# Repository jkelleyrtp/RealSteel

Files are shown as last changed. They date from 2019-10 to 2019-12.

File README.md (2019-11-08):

# FA19_POE_Final
Shadow-boxing robot using real-time pose estimation and a forward kinematic solver.

An exercise in high-speed Python, computer vision, point clouds, hardware iteration, and project management. 

Our public OnShape model is here:
    https://cad.onshape.com/documents/69187161d3d30544dff47cbf/w/b6740c08ed5948e4f2cbee36/e/f1060944df77cc7be88ce15a

## blog
The source files for the Hugo site generator.

## docs
The output of the hugo site generator

## scripts
Scripts to run various parts of the stack. All scripts are meant to be launched from the top level directory.

- `publishsite.sh` rebuilds the hugo site and pushes it to docs
- `launchapp.sh` runs python app in the correct environment

## robot
The DOF model for the robot to be displayed

## src
Primary application that runs the real steel experience.

## firmware
Firmware running on the microncontroller that responds to commands from app

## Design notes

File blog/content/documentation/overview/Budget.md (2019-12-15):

+++
title = "Budget"
weight = 40
+++

<center>

<table>
<tr>
<th>Item</th>
<th>Quantity</th>
<th>Price Per</th>
<th>Price Total</th>
</tr>
<tr>
<td>DC Motor 200 RPM</td>
<td>6</td>
<td>$15</td>
<td>$90</td>
</tr>
<tr>
<td>DC Motor Controller</td>
<td>6</td>
<td>$4</td>
<td>$24</td>
</tr>
<tr>
<td>5mm Shaft</td>
<td>2</td>
<td>$8</td>
<td>$16<br></td>
</tr>
<tr>
<td>3mm Shaft</td>
<td>1</td>
<td>$7</td>
<td>$7</td>
</tr>
<tr>
<td>M5 Bearing</td>
<td>4</td>
<td>$5</td>
<td>$20</td>
</tr>
<tr>
<td>M3 Bearing</td>
<td>10</td>
<td>$7</td>
<td>$70</td>
</tr>
<tr>
<td>Encoder</td>
<td>6</td>
<td>$2</td>
<td>$12</td>
</tr>
<tr>
<td>Hardware Kit</td>
<td>1</td>
<td>$15</td>
<td>$10</td>
</tr>
<tr>
<td>Total:</td>
<td></td>
<td></td>
<td>$249</td>
</tr>
<tr>
<td></td>
<td></td>
<td></td>
<td></td>
</tr>
<tr>
<td></td>
<td></td>
<td></td>
<td></td>
</tr>
</table>

</center>

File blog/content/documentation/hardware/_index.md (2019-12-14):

+++
title = "Hardware"
weight = 2
sort_by = "weight"
redirect_to = "documentation/content/overview"
insert_anchor_links = "left"
+++

Hardware
- High-level design
- Base
- Torso
- Arm
- Assembly

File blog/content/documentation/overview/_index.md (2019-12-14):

+++
title = "Overview"
weight = 1
sort_by = "weight"
redirect_to = "documentation/overview/overview"
insert_anchor_links = "left"
+++

Overview
 - Inspiration
 - Brainstorming
 - Constraints
 - Systems Design
 - Budget

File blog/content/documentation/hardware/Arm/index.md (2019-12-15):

+++
title = "Arm Design"
weight = 40
+++

The Real Steel robot arms were some of the most fun pieces to design of the whole system. We wanted to keep the mass of the arm as close to the axis of rotation as possible - the more balanced the arms were, the faster the motors could turn them. 

## Top-Level design

To simplify the design of the complicated sensor and motor interfaces, we created a single top-level sketch of the entire robot system and derived sketches for each of the subsystems. This approach to design is a common parametric technique that allows upstream design changes without breaking everything downstream. We were able to iterate on the width of the robot's shoulders and shoulder angles while the final pieces remained relatively the same. The benefits of this approach came to fruition when we modified the arm dimensions and mass in the final sprint by changing just a few numbers and reprinting all the pieces. 

We were particularly careful to keep the mass and size of the arm to a minimum. We gave special consideration to the placement of the servo and kept the center of mass as close to the shaft axis of rotation as possible. This gave the arm a fairly low mass moment of angular inertia. We used a simple linkage to transfer the servo's torque to the elbow which kept the weight down and allowed us to get a simple torque multiplier in with little effort. By maintaining a low profile on the arm components, the robot had a greater range of motion and could move fast enough for real-time movements. 

<center> {{ resize_image(path="documentation/hardware/Arm/Untitled.png", width=0, height=500, op="fit_height") }} </center>

<div class="row">
  <div class="column">
    <center> {{ resize_image(path="documentation/hardware/Arm/Untitled 3.png", width=0, height=300, op="fit_height") }} </center>
  </div>
  <div class="column">
    <center> {{ resize_image(path="documentation/hardware/Arm/Untitled 1.png", width=0, height=300, op="fit_height") }} </center>
  </div>
</div>

We were also careful to design with failure in mind. At the major interfaces, we chose to separate the single part into two parts fastened together. Specifically for the arm, the hub that connected it to the driving motor was removable from the primary arm component. We happened to print the dimensions improperly a few times before getting the design dialed in, and the separation between hub and arm was vital to keep the iteration time as fas as possible.

<center> {{ resize_image(path="documentation/hardware/Arm/Untitled 2.png", width=0, height=500, op="fit_height") }} </center>

<style>
    .row {
    display: flex;
    }

    .column {
    flex: 50%;
    }
</style>

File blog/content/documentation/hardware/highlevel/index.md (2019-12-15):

+++
title = "High Level Design"
weight = 10
+++

We faced a significant challenge in integrating the mechanical and electrical aspects of the project; each additional component added more complexity and points of failure. To mitigate the potential non-obvious potholes, we decided to start designing the system from a high-level first before diving into the details. 

Our mechanical system had a handful of requirements:

- The ability to "throw a punch"
- The ability to "bob and weave"
- The ability to "block a punch"

This ultimately manifested itself into a robot with:

- Two arms
- 3 DoF per arm (shoulder, proximal, and distal)
- 2 DoF hip system

Using OnShape as our CAD software of choice, we sketched out the high-level geometry, making sure to maintain realistic dimensions and leave room for important components like servos, motors, and sensors. The system sketch was used in "derive" mode to generate the rest of the subsystems.

<center> {{ resize_image(path="documentation/hardware/highlevel/Untitled.png", width=0, height=500, op="fit_height") }} </center>

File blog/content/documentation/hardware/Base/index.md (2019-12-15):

+++
title = "Base Design"
weight = 20
+++

The base of the robot underwent significant development. Early revisions were severely underspecced and not strong enough to hold the weight of the entire bot. 

The final design included 2 degrees of freedom - one for side-to-side movements and one for forward-to-backward movements - essentially pitch and roll. The dual fourbar design allowed the robot to move in both directions at once with design inspiration from joysticks. We used potentiometers to get feedback from the fourbars and a interesting method of embedded shaft to strength the prints.

<center> {{ resize_image(path="documentation/hardware/Base/Untitled.png", width=0, height=500, op="fit_height") }} </center>

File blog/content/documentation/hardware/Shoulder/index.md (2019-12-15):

+++
title = "Shoulder Design"
weight = 35
+++

The shoulders of the Real Steel robots were fun to design and pulled in some interesting 3D print techniques. We created an adapter system that used the profile of the motor shafts to fasten the hubs onto the primary body parts. This let us gracefully handle failures and more easily replace broken components. We also designed and 3D-printed our own gears which were used in conjunction with the custom encoder boards to get position feedback of the joints back to the STM32 controller. 

<div class="row">
  <div class="column">
    <center> {{ resize_image(path="documentation/hardware/Shoulder/Untitled.png", width=0, height=500, op="fit_height") }} </center>
  </div>
  <div class="column">
    <center> {{ resize_image(path="documentation/hardware/Shoulder/Untitled 2.png", width=0, height=500, op="fit_height") }} </center>
  </div>
</div>

<style>
    .row {
    display: flex;
    }

    .column {
    flex: 50%;
    }
</style>

One of the most interesting components of the shoulder system was the design of a custom parametric slew bearing which could adapt to any size we needed. We stuck with one size and honed in the sizes to be amenable for 3D printing. The slew bearings were able to take high axial and radial loads and were fast to manufacture. 

<center> {{ resize_image(path="documentation/hardware/Shoulder/Untitled 1.png", width=0, height=300, op="fit_height") }} </center>

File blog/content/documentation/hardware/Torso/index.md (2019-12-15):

+++
title = "Torso Design"
weight = 30
+++

The torso of the Real Steel robots was one of the more complicated parts of the robot to design. Not only did it have to integrate with the robot base, but it had to support both arms, the head, and the accompanying sensors to maintain accurate position control over the shoulder joints. The final design of the robot body came together in 5 separate pieces: the torso, the shoulder supports, the stand balance plate, and the head. 

The adapter plate was designed to simply bolt into the bottom of the primary torso part. We iterated several times on the adapter plate to allow for the "bob" and "weave" ranges of motion, and settled on the adapter plate design to allow for modifications to be made without having to reprint the torso. in fact, the torso itself is 3 separate pieces fastened together with bolts, plastic inserts, and CA glue.

<center>
    {{ resize_image(path="documentation/hardware/Torso/Untitled.png", width=0, height=500, op="fit_height") }}
</center>

We spent a lot of time iterating on the placement of motors and sensors on the torso. Shown below is the strange placement of the shoulder motor embedded deep into the torso. The wires were mostly inaccessible and had to be wired and soldered before installation. For proper assembly, the motor had to be dropped into the torso, the shoulder mound had to be fastened, and then we could finally mount the motor to the rest of the shoulder. However, the final design was very strong and with clever 3D printing, we achieved a robust torso design operating at near maximum PLA strength (more in some areas!) that gracefully took a few falls off the assembly table.

<center>
    {{ resize_image(path="documentation/hardware/Torso/Untitled 1.png", width=0, height=500, op="fit_height") }}
</center>

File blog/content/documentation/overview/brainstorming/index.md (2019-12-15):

+++
title = "Brainstorming + Inspiration"
weight = 20
+++

The idea to create a shadow boxing robot was nearly instant on the first team brainstorming night. Our  learning goals imposed an intense set of requirements on the project:

Machine Learning - Use AI/ML to provide a powerful HCI experience

Mechanical Iteration - Fabricate several iterations of a hardware-focused project

Kinematics - Do some complicated parallel math to build concurrency skills

Firmware - Use higher-end embedded architectures ARM/STM32

Closed-loop control - Implement a predictive control algorithm

Project Management - Get things done on time!

We ideated in one night, coming up with a handful of different projects we thought might properly satisfy the design constraints (notice the 5th idea):

<center>
    {{ resize_image(path="documentation/overview/Brainstorming/Untitled.png", width=0, height=500, op="fit_height") }}
</center>

## Night 1 Ideation

We initially imagined the shadow boxing robot as a pair of fighters - similar to the rock-em-sock robot game. Ultimately, we settled on a single fighter with a similar range of motion to that of the robots in the movie "Real Steel" - the 2011 action flick of the summer with Hugh Jackman and Dakota Goyo - one of our all-time personal favorite movies.

<center>
<div>

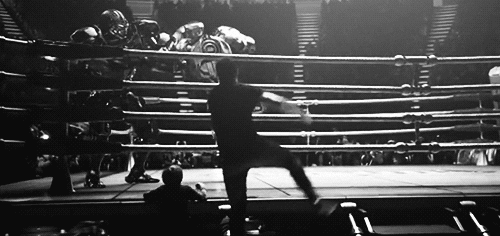
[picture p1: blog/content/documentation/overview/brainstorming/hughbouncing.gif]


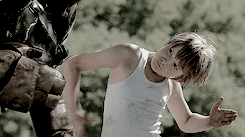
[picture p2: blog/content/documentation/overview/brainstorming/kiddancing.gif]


</div>
</center>

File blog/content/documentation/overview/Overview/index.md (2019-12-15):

+++
title = "Overview"
weight = 10
+++

This documentation provides a set of information and resources on how to design, build, and program and shadow-boxing robot for less than $250. This was an exceptionally ambitious Principles of Engineering project and required advanced skills in CAD, CAM, math, firmware, software, and systems integration. Each component of the system -  whether it be the serial output format of the robot joints or the location of the elbow linkage - was dependent on the other components. This led to an incredibly carefully designed collection of components that pushed the limits of Olin's 3D printers, the STM32 microcontroller, and the compute power of the school laptops. 

<center>
    {{ resize_image(path="documentation/overview/overview/reaganbot.png", width=0, height=500, op="fit_height") }}
</center>

## Final Feature Set

The final featureset of the Real Steel shadow-boxing robot is quite amazing:

- 8 Degrees of freedom - two arms and a hip system
- The ability to bob, weave, throw punches, and dab, all in real time
- 8 real-time PID controllers maintaining closed-loop control of the robot joint positions
- Real time pose estimation using a Time-of-Flight depth sensor
- Real-time kinematic solving of a 3 DoF robotic arm from a human's 7 DoF
- A portable Python-based multithreaded framework for data collection, processing, visualization, and serial output
- Pre-programmed positions for control without the kinect

## Challenges and Constraints

We ran into several challenges while designing and building the Real Steel robot. These included:

- Limited microcontroller inputs 12 quadrature encoders (2 robots worth, ran out after 1 robot)
- Limited outputs to control all the motor outputs
- Limited electrical power to power all motors simultaneously
- Limited compute power to process the kinect data and convert it into a serial packet with joint information
- Limited mechanical strength on 3D printed parts to handle the forces involved in moving the robot around

The following sections address these challenges and provide further insights on how the final feature set came together.

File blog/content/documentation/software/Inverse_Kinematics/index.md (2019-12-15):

+++
title = "Inverse Kinematics"
weight = 30
+++

## Inverse Kinematics

Inverse Kinematics is needed to map human movement into robot movement. This is because, calculating joint angles using human extracted joints doesn't translate to robot joint angles. We have different joints than the robot and at different positions and lengths. Instead, using an inverse kinematics solver an articulated body can be programmed to reach a certain target position with its end effector.

<center>


</center>

In RealSteel's robots, we have the following revolute joints in an arm:

1. Shoulder
2. Proximal
3. Distal

<center>
    {{ resize_image(path="documentation/software/Inverse_Kinematics/Untitled.png", width=0, height=500, op="fit_height") }}
</center>

### How Does It Work?

Given a target position, how can we position the articulated body and all it's joints such that the end effector reaches the target? An inverse kinematics solver answers this question with two categories of solutions:

1. Analytic solutions
2. Approximating solutions

We use ikpy, an inverse kinematics library, that can quickly approximate the solution with an iterative optimizer with regularization for smoothing.

<center>
    {{ resize_image(path="documentation/software/Inverse_Kinematics/Untitled 1.png", width=0, height=500, op="fit_height") }}
</center>

ikpy also can import the kinematic chain to solve as long as the robot is defined in URDF format. Luckily for us, we designed our own robot in OnShape and using onshape-to-robot we can convert our OnShape assembly to URDF robot definition.

### ikpy Coordinate System

ikpy defines its kinematic chain to start at the origin in a coordinate system that is rotated 90° about the x-axis compared to the Kinect coordinate system. We also run into an issue as the Kinect tracks joint positions with respect to a fixed origin at the center of it's camera lens and not at the base of the kinematic chain - the origin that ikpy expects. Therefore, any target position that we want to solve for with ikpy will be misinterpreted.

The solution is to transform the target joint's (the hand joint) position from the Kinect frame to a frame that has it's origin fixed at the shoulder joint of the arm that is being solved for. The z or depth value is then inverted to place depth in front of the person, and the point is rotated 90° about the x-axis. This way now the kinematic chain and target joint position are in the same frame of reference, and ikpy can solve correctly.

<center>
    {{ resize_image(path="documentation/software/Inverse_Kinematics/Untitled 2.png", width=0, height=400, op="fit_height") }}
</center>

### The Process

With all the tools in place, we can now proceed with solving for our robot joint angles in real-time in the following steps (note: this is done independently for both arms each)

1. Obtain robot model in URDF format
2. Import model into ikpy and define a base_element to start the kinematic chain at the shoulder joint of an arm
3. Obtain target position from the Kinect → the world coordinates for skeletal joint at the hand for the corresponding arm
4. Perform the necessary transforms to get the target into ikpy coordinate system
5. Solve for joint angles

[https://youtu.be/kSUGiyJ5UbY](https://youtu.be/kSUGiyJ5UbY)

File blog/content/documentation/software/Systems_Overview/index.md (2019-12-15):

+++
title = "Software Overview"
weight = 10
+++

The software powering Real Steel is fairly complex, but we chose a handful of architectural patterns and libraries to simplify the development process. Our language of choice was Python and we relied heavily on `OpenNI` for kinect-related libraries, Python's `Multiprocessing` library for concurrency, `ikpy` for forward kinematic solving, `pybullet` for simulation of the robot, and `PySerial` to get the joint angle to the robot.

<center>
    {{ resize_image(path="documentation/software/Systems_Overview/Untitled.png", width=0, height=500, op="fit_height") }}
</center>

All of these components were given their own `class` in the Python code, and inherited certain functionality so that we could easily disable and enable different parts of the code with a few flags. For instance, the python code that loads in all the modules is fairly simple, despite the entire codebase being several thousand lines. We chose the pipeline architecture and separated each of the components into their own submodules to be more easily unit-testable. The entire system can run with "fake" components which satisfy the software requirements and even create fake data so we can do integration tests with entire chunks of the pipeline missing. This is a solid, industry-practiced software engineering tactic that allowed us to iterate faster and modularize our code.

```python
from realsteel.device import ROBOT_DEVICE, FAKE_DEVICE
from realsteel.visualizer import DEMO_VIS, ROBOT_VIS, FAKE_VIS
from realsteel.joint_input import CAMERA, KINECT, HYBRID
from realsteel.kinematic import KSOLVER
from realsteel.pathplanner import PATHPLANNER
from realsteel.kinematic import ArmJoints

class ROBOT:
    """
    This code processes the launch args and sets up all the moving parts to get the REAL STEEL experience up and running.
    Nothing in this main loop should blocking, but rather pushing data around between threads. Everything should be async.

    """
    def __init__(self, hardware_enabled = False, visualization_mode="disabled"):
        # [1] Build the virtual robot from joints
        # [2] Set up the camera/kinect inputs to dump raw joint angles
        # [3] Set up the kinematic solver that takes raw joint angles and turns into robot angles
        # [4] Set up the path planner that maps joint angles frames
        # [5] Set up the physical robot interface
        # [6] Set up the visualizer

        # Process the user flags to process things like dev mode
        self.hardware_enabled: bool = hardware_enabled
        self.visualization_mode = visualization_mode

        # [1] Build the robot from a URDF file
        # TODO, allow specifying a custon URDF
        self.human_positions: dict = None
        self.robot_positions: dict = None
        # self.intialize_robot_from_urdf(file = "")

        # [2] Set up the camera/kinect input device
        self.joint_input = HYBRID()

        # [3] Set up the kinematic solver 
        self.solver = KSOLVER()

        # [4] Set up the path planner
        self.planner = PATHPLANNER()

        # [5] Set up the hardware device
        if self.hardware_enabled:
            self.device = ROBOT_DEVICE()
        else:
            self.device = FAKE_DEVICE()

        # [6] Set up the visualizer
        if self.visualization_mode == "dev":
            self.visualizer = ROBOT_VIS(directory='robot/')

        elif self.visualization_mode == "demo":
            self.visualizer = DEMO_VIS()

        else:
            self.visualizer = FAKE_VIS()
```

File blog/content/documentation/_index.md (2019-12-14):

+++
template = "documentation.html"
redirect_to = "documentation/overview/"
+++

Overview
Overview
Inspiration
Brainstorming
Constraints
Systems Design
Budget
 
Hardware
High-level design
Base
Torso
Arm
Assembly

Electrical and Firmware
Sensors
Schematic
Firmware overview
Control loops and feedback

Software
Human Tracking
PyBullet
Kinematics Tracking
Multithreading
Serial Output

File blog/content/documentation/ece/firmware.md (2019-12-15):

+++
title = "Firmware Overview"
weight = 10
+++

The robot firmware had one job: take a setpoint over serial and maintain closed-loop control over the robot subsystems. We used PWM to communicate with each of the motor controllers and an external power supply to power everything, so the firmware simply needed to output a signal for each motor. 

The setpoint came in over serial and was decoded by a custom bson interpreter written in C++. We used the STM32 chip on the Nucleo F446ZE development board as the microcontroller, and reused PID control from the last PoE lab for closed-loop control. As our port and compute capacity was limited, the predictive control was all implemented on the host software.

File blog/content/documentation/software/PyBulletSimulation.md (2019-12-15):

+++
title = "PyBullet Simulation"
weight = 40
+++

## PyBullet Simulation

Before we send the joint coordinates over serial to the actual robot, we want to ensure that our methodology and solutions are correct. Therefore, we use PyBullet, a physics engine, to simulate our robot movements.

<center>
    {{ resize_image(path="documentation/software/Inverse_Kinematics/Untitled 3.png", width=0, height=200, op="fit_height") }}
</center>

Loading in our URDF file for the robot, we can pump in the joint angles and see how a virtual replica of our robot would behave under proper physics.

[https://youtu.be/1XufNJylf4Q](https://youtu.be/1XufNJylf4Q)

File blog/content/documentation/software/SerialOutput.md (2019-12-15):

+++
title = "Serial Output"
weight = 60
+++

To communicate with the Real Steel robots, we initialized a serial interface with the STM32 microcontroller (the robot's brain) to send joint positions and other information. We set up the serial interface in a separate thread as to not slow down the main thread responsible for moving data in between each of the system components. This let us maintain a 1 kHz control loop between the master computer and Real Steel robot without any performance impact on the rest of the software system.

To communicate, we used the bson minified data format - a compressed version of csv with a fixed schema based on packet length. We also developed a custom interpreter for the STM32 as there were no obvious choices that fit on an embedded system to interpret the serial data. The final format for commands between the computer and robot followed as such:

```rust
#[derive(debug, fmt)]
enum MessageTypes {
	setpoint(RobotSetpoint)
}

impl serialize for MessageTypes {
	fn serialize() -> String {
		match Self {
			MessageTypes::setpoint(setpoint) -> {
				return format!(
					"0",
					setpoint.left_shoulder,
					setpoint.left_proximal,
					setpoint.left_distal: usize,
					setpoint.right_shoulder,
					setpoint.right_proximal,
					setpoint.right_distal,
					pitch: usize,
					roll: uszie
				)
			}
		}
	}
}

#[derive(debug, fmt)]
struct RobotSetpoint {
	left_shoulder: usize,
	left_proximal: usize,
	left_distal: usize,
	right_shoulder: usize,
	right_proximal: usize,
	right_distal: usize,
	pitch: usize,
	roll: uszie
}
```

With this format, we could easily serialize and deserialize robot setpoints from the kinematic solver and convert them into a message that the robot could interpret. Messages could be of variable length, with the expected length determined by the leading digit for the packet. As shown above, the leading digit for the RobotSetpoint is 0 - so the stm32 can easily decode the robot position over a simple serial packet.

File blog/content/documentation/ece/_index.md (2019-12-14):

+++
title = "Electrical and Firmware"
weight = 3
sort_by = "weight"
redirect_to = "documentation/ece/Firmwareoverview"
insert_anchor_links = "left"
+++

Overview
 - Inspiration
 - Brainstorming
 - Constraints
 - Systems Design
 - Budget

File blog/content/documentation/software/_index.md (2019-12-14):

+++
title = "Software"
weight = 1
sort_by = "weight"
redirect_to = "documentation/software/overview.md"
insert_anchor_links = "left"
+++

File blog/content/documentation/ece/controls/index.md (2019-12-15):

+++
title = "Controls and Feedback"
weight = 30
+++

## Motor control:

A simple PID controller was used for motor control. However, we were able to run it at 1kHz due to the floating point accelerator on the STM32F446, allowing for extremely high gain feedback.

## Motor controller boards:

We decided to be thrifty and copied 1:1 Adafruit's DRV8871 motor controller boards, saving us a large amount of money compared to what we'd have to spend on 12 genuine ones.

<center> {{ resize_image(path="documentation/ece/controls/Untitled.png", width=0, height=500, op="fit_height") }} </center>

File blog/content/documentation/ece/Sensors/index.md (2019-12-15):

+++
title = "Sensors"
weight = 20
+++

We designed a handful of custom sensor to make the feedback collection easier. One important sensor we designed was a simple quadrature encoder board with a dial knob. This allowed us to integrate the gears onto the encoders with ease, and each board was exceptionally cheap at only $2 per.

<center> {{ resize_image(path="documentation/ece/Sensors/Untitled.png", width=0, height=500, op="fit_height") }} </center>

As 8 quadrature encoders is simply too much information for the STM32 to handle at once, we also developed a simple quadrature interpreter board after we had designed the quadrature encoders. This counted the number of steps the quadrature encoder had performed and stored them so the firmware wouldn't have to keep track manually. These boards were powered by a simple STM8 and output their data over I2C. This gave us an incredible performance boost and allowed us to keep closed-loop control of the robot arms and hip system without the controller breaking a sweat.

<center> {{ resize_image(path="documentation/ece/Sensors/Untitled 1.png", width=0, height=500, op="fit_height") }} </center>

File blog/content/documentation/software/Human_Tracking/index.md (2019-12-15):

+++
title = "Human Tracking"
weight = 20
+++

## Human Tracking

We use the Kinect v1 camera to perform human skeleton tracking using its IR camera. We interface with the Kinect using the OpenNI2 library for core Kinect features and NiTE2 for skeleton tracking purposes. To support the Kinect v1 camera with these two libraries, the OpenNI2-FreenectDriver bridge must also be installed. These libraries allow us to develop in non-windows platforms using opensource software.

### Dependency Installation

There are difficulties in getting these dependencies installed as the OpenNI and NiTE project was discontinued when Apple bought PrimeSense. Instead, these packages are now hosted and can be downloaded using the following guide:

[https://github.com/roboticslab-uc3m/installation-guides/blob/master/install-openni-nite.md](https://github.com/roboticslab-uc3m/installation-guides/blob/master/install-openni-nite.md)

### Skeleton Tracking

Using NiTE2 we access skeleton tracking information from the Kinect. At each frame we obtain the position of all 15 joints as (x, y, z) coordinates. 

<center>

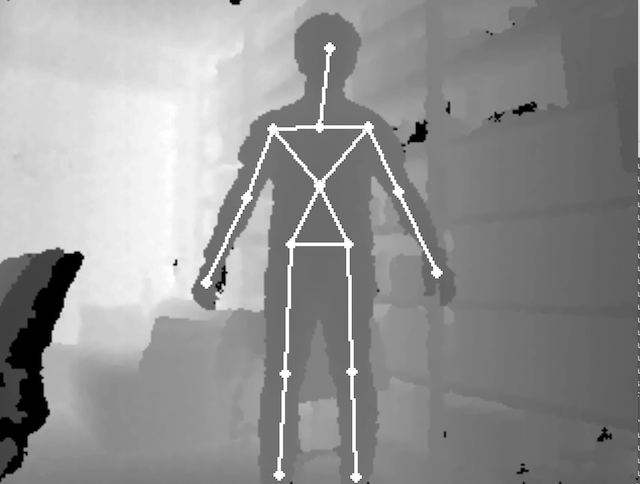
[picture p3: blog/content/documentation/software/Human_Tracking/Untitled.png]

</center>

### Coordinate System

The Kinect and OpenNI has two coordinate systems used. These two systems are referred to as Depth and World representation. The differences can be described like so:

1. Depth coordinates
    - the native data representation
    - the origin is the top-left corner of the field of view
    - x and y coordinates are reference to the image frame pixels
    - the depth value represents the distance between the camera plane and whatever object is in the given pixel
2. World coordinates
    - superimpose a more familiar 3D Cartesian coordinate system on the world
    - the origin is at the Kinect camera lens
    - every point is specified by 3 points (x, y , z) in millimeters

<center>

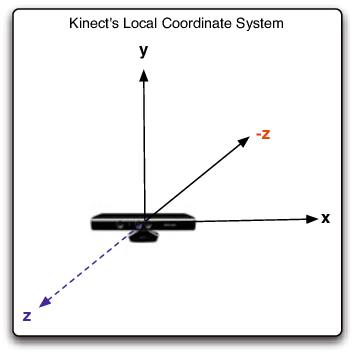
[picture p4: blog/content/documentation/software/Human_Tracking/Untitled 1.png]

</center>

We obtain the joint information and can convert between both systems depending on our needs.

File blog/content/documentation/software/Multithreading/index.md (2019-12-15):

+++
title = "Multithreaded Framework"
weight = 50
+++

## Multithreaded Framework

In order to perform the skeleton tracking, joint solving, visualizations, and communication all together  simultaneously, we set up a multithreaded framework centered around python's multiprocessing Queues. In our framework, we use two queues: an input queue and a device/output queue. 

The input queue gets Kinect joint information pushed into it at every frame. The other systems, inverse kinematics and visualizations, pop joint information off of this queue as long as it's not empty for processing.

The device queue gets robot joint angles pushed into it at every iteration of the main robot loop and communicates these angles over serial whenever they are available.

```python
def main_loop(self):
	# Set up a shared queue to put human angles into
	input_queue = Queue()

	# Get the process for the input method and start it
	input_proc = self.joint_input.launch(input_queue)
	input_proc.start()
	
	# Set up the device queue to push data into
	device_queue = Queue()
	device_proq = self.device.launch(device_queue)
	device_proq.start()
	
	# Set the initial joint angles
	joints = {}
	joint_angles = [1, 1]
	
	while True:
		# Check if there's a new human joint inputs ready
		# if not input_queue.empty():
		joints = input_queue.get()
		if joints['Lwri']:
			joint_angles = self.solver.solve(joints['Lwri']['pc'])
	
			joint = ArmJoints(joint_angles[0], joint_angles[1], 0.0)
	
			device_queue.push(joint)
```

This architecture is the exact same architecture used in microprocessors and the technique is known as "pipelining." Just by properly designing the architecture of our code, we saw up to 60-80% performance improvement which was crucial for real time actuation.

<center>
    {{ resize_image(path="documentation/software/Multithreading/Untitled.png", width=0, height=500, op="fit_height") }}
</center>

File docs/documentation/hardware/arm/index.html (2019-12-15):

- Overview
  - Overview (https://jonathan-kelley.com/FA19_POE_Final/documentation/overview/overview/)
  - Brainstorming + Inspiration (https://jonathan-kelley.com/FA19_POE_Final/documentation/overview/brainstorming/)
  - Budget (https://jonathan-kelley.com/FA19_POE_Final/documentation/overview/budget/)
- Software
  - Software Overview (https://jonathan-kelley.com/FA19_POE_Final/documentation/software/systems-overview/)
  - Human Tracking (https://jonathan-kelley.com/FA19_POE_Final/documentation/software/human-tracking/)
  - Inverse Kinematics (https://jonathan-kelley.com/FA19_POE_Final/documentation/software/inverse-kinematics/)
  - PyBullet Simulation (https://jonathan-kelley.com/FA19_POE_Final/documentation/software/pybulletsimulation/)
  - Multithreaded Framework (https://jonathan-kelley.com/FA19_POE_Final/documentation/software/multithreading/)
  - Serial Output (https://jonathan-kelley.com/FA19_POE_Final/documentation/software/serialoutput/)
- Hardware
  - High Level Design (https://jonathan-kelley.com/FA19_POE_Final/documentation/hardware/highlevel/)
  - Base Design (https://jonathan-kelley.com/FA19_POE_Final/documentation/hardware/base/)
  - Torso Design (https://jonathan-kelley.com/FA19_POE_Final/documentation/hardware/torso/)
  - Shoulder Design (https://jonathan-kelley.com/FA19_POE_Final/documentation/hardware/shoulder/)
  - Arm Design (https://jonathan-kelley.com/FA19_POE_Final/documentation/hardware/arm/)
  - Assembly (https://jonathan-kelley.com/FA19_POE_Final/documentation/hardware/assembly/)
- Electrical and Firmware
  - Firmware Overview (https://jonathan-kelley.com/FA19_POE_Final/documentation/ece/firmware/)
  - Sensors (https://jonathan-kelley.com/FA19_POE_Final/documentation/ece/sensors/)
  - Controls and Feedback (https://jonathan-kelley.com/FA19_POE_Final/documentation/ece/controls/)

# Arm Design

The Real Steel robot arms were some of the most fun pieces to design of the whole system. We wanted to keep the mass of the arm as close to the axis of rotation as possible - the more balanced the arms were, the faster the motors could turn them.

## 🔗Top-Level design

To simplify the design of the complicated sensor and motor interfaces, we created a single top-level sketch of the entire robot system and derived sketches for each of the subsystems. This approach to design is a common parametric technique that allows upstream design changes without breaking everything downstream. We were able to iterate on the width of the robot's shoulders and shoulder angles while the final pieces remained relatively the same. The benefits of this approach came to fruition when we modified the arm dimensions and mass in the final sprint by changing just a few numbers and reprinting all the pieces.

We were particularly careful to keep the mass and size of the arm to a minimum. We gave special consideration to the placement of the servo and kept the center of mass as close to the shaft axis of rotation as possible. This gave the arm a fairly low mass moment of angular inertia. We used a simple linkage to transfer the servo's torque to the elbow which kept the weight down and allowed us to get a simple torque multiplier in with little effort. By maintaining a low profile on the arm components, the robot had a greater range of motion and could move fast enough for real-time movements.







We were also careful to design with failure in mind. At the major interfaces, we chose to separate the single part into two parts fastened together. Specifically for the arm, the hub that connected it to the driving motor was removable from the primary arm component. We happened to print the dimensions improperly a few times before getting the design dialed in, and the separation between hub and arm was vital to keep the iteration time as fas as possible.



©2017-2019 — Jonathan Kelley (https://jonathan-kelley.com) and contributors (https://github.com/jkelleyrtp/FA19_POE_Final/graphs/contributors)

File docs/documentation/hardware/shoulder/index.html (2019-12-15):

- Overview
  - Overview (https://jonathan-kelley.com/FA19_POE_Final/documentation/overview/overview/)
  - Brainstorming + Inspiration (https://jonathan-kelley.com/FA19_POE_Final/documentation/overview/brainstorming/)
  - Budget (https://jonathan-kelley.com/FA19_POE_Final/documentation/overview/budget/)
- Software
  - Software Overview (https://jonathan-kelley.com/FA19_POE_Final/documentation/software/systems-overview/)
  - Human Tracking (https://jonathan-kelley.com/FA19_POE_Final/documentation/software/human-tracking/)
  - Inverse Kinematics (https://jonathan-kelley.com/FA19_POE_Final/documentation/software/inverse-kinematics/)
  - PyBullet Simulation (https://jonathan-kelley.com/FA19_POE_Final/documentation/software/pybulletsimulation/)
  - Multithreaded Framework (https://jonathan-kelley.com/FA19_POE_Final/documentation/software/multithreading/)
  - Serial Output (https://jonathan-kelley.com/FA19_POE_Final/documentation/software/serialoutput/)
- Hardware
  - High Level Design (https://jonathan-kelley.com/FA19_POE_Final/documentation/hardware/highlevel/)
  - Base Design (https://jonathan-kelley.com/FA19_POE_Final/documentation/hardware/base/)
  - Torso Design (https://jonathan-kelley.com/FA19_POE_Final/documentation/hardware/torso/)
  - Shoulder Design (https://jonathan-kelley.com/FA19_POE_Final/documentation/hardware/shoulder/)
  - Arm Design (https://jonathan-kelley.com/FA19_POE_Final/documentation/hardware/arm/)
  - Assembly (https://jonathan-kelley.com/FA19_POE_Final/documentation/hardware/assembly/)
- Electrical and Firmware
  - Firmware Overview (https://jonathan-kelley.com/FA19_POE_Final/documentation/ece/firmware/)
  - Sensors (https://jonathan-kelley.com/FA19_POE_Final/documentation/ece/sensors/)
  - Controls and Feedback (https://jonathan-kelley.com/FA19_POE_Final/documentation/ece/controls/)

# Shoulder Design

The shoulders of the Real Steel robots were fun to design and pulled in some interesting 3D print techniques. We created an adapter system that used the profile of the motor shafts to fasten the hubs onto the primary body parts. This let us gracefully handle failures and more easily replace broken components. We also designed and 3D-printed our own gears which were used in conjunction with the custom encoder boards to get position feedback of the joints back to the STM32 controller.





One of the most interesting components of the shoulder system was the design of a custom parametric slew bearing which could adapt to any size we needed. We stuck with one size and honed in the sizes to be amenable for 3D printing. The slew bearings were able to take high axial and radial loads and were fast to manufacture.



©2017-2019 — Jonathan Kelley (https://jonathan-kelley.com) and contributors (https://github.com/jkelleyrtp/FA19_POE_Final/graphs/contributors)

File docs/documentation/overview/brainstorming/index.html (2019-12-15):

- Overview
  - Overview (https://jonathan-kelley.com/FA19_POE_Final/documentation/overview/overview/)
  - Brainstorming + Inspiration (https://jonathan-kelley.com/FA19_POE_Final/documentation/overview/brainstorming/)
  - Budget (https://jonathan-kelley.com/FA19_POE_Final/documentation/overview/budget/)
- Software
  - Software Overview (https://jonathan-kelley.com/FA19_POE_Final/documentation/software/systems-overview/)
  - Human Tracking (https://jonathan-kelley.com/FA19_POE_Final/documentation/software/human-tracking/)
  - Inverse Kinematics (https://jonathan-kelley.com/FA19_POE_Final/documentation/software/inverse-kinematics/)
  - PyBullet Simulation (https://jonathan-kelley.com/FA19_POE_Final/documentation/software/pybulletsimulation/)
  - Multithreaded Framework (https://jonathan-kelley.com/FA19_POE_Final/documentation/software/multithreading/)
  - Serial Output (https://jonathan-kelley.com/FA19_POE_Final/documentation/software/serialoutput/)
- Hardware
  - High Level Design (https://jonathan-kelley.com/FA19_POE_Final/documentation/hardware/highlevel/)
  - Base Design (https://jonathan-kelley.com/FA19_POE_Final/documentation/hardware/base/)
  - Torso Design (https://jonathan-kelley.com/FA19_POE_Final/documentation/hardware/torso/)
  - Shoulder Design (https://jonathan-kelley.com/FA19_POE_Final/documentation/hardware/shoulder/)
  - Arm Design (https://jonathan-kelley.com/FA19_POE_Final/documentation/hardware/arm/)
  - Assembly (https://jonathan-kelley.com/FA19_POE_Final/documentation/hardware/assembly/)
- Electrical and Firmware
  - Firmware Overview (https://jonathan-kelley.com/FA19_POE_Final/documentation/ece/firmware/)
  - Sensors (https://jonathan-kelley.com/FA19_POE_Final/documentation/ece/sensors/)
  - Controls and Feedback (https://jonathan-kelley.com/FA19_POE_Final/documentation/ece/controls/)

# Brainstorming + Inspiration

The idea to create a shadow boxing robot was nearly instant on the first team brainstorming night. Our learning goals imposed an intense set of requirements on the project:

Machine Learning - Use AI/ML to provide a powerful HCI experience

Mechanical Iteration - Fabricate several iterations of a hardware-focused project

Kinematics - Do some complicated parallel math to build concurrency skills

Firmware - Use higher-end embedded architectures ARM/STM32

Closed-loop control - Implement a predictive control algorithm

Project Management - Get things done on time!

We ideated in one night, coming up with a handful of different projects we thought might properly satisfy the design constraints (notice the 5th idea):



## 🔗Night 1 Ideation

We initially imagined the shadow boxing robot as a pair of fighters - similar to the rock-em-sock robot game. Ultimately, we settled on a single fighter with a similar range of motion to that of the robots in the movie "Real Steel" - the 2011 action flick of the summer with Hugh Jackman and Dakota Goyo - one of our all-time personal favorite movies.





©2017-2019 — Jonathan Kelley (https://jonathan-kelley.com) and contributors (https://github.com/jkelleyrtp/FA19_POE_Final/graphs/contributors)

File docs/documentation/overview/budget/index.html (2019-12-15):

- Overview
  - Overview (https://jonathan-kelley.com/FA19_POE_Final/documentation/overview/overview/)
  - Brainstorming + Inspiration (https://jonathan-kelley.com/FA19_POE_Final/documentation/overview/brainstorming/)
  - Budget (https://jonathan-kelley.com/FA19_POE_Final/documentation/overview/budget/)
- Software
  - Software Overview (https://jonathan-kelley.com/FA19_POE_Final/documentation/software/systems-overview/)
  - Human Tracking (https://jonathan-kelley.com/FA19_POE_Final/documentation/software/human-tracking/)
  - Inverse Kinematics (https://jonathan-kelley.com/FA19_POE_Final/documentation/software/inverse-kinematics/)
  - PyBullet Simulation (https://jonathan-kelley.com/FA19_POE_Final/documentation/software/pybulletsimulation/)
  - Multithreaded Framework (https://jonathan-kelley.com/FA19_POE_Final/documentation/software/multithreading/)
  - Serial Output (https://jonathan-kelley.com/FA19_POE_Final/documentation/software/serialoutput/)
- Hardware
  - High Level Design (https://jonathan-kelley.com/FA19_POE_Final/documentation/hardware/highlevel/)
  - Base Design (https://jonathan-kelley.com/FA19_POE_Final/documentation/hardware/base/)
  - Torso Design (https://jonathan-kelley.com/FA19_POE_Final/documentation/hardware/torso/)
  - Shoulder Design (https://jonathan-kelley.com/FA19_POE_Final/documentation/hardware/shoulder/)
  - Arm Design (https://jonathan-kelley.com/FA19_POE_Final/documentation/hardware/arm/)
  - Assembly (https://jonathan-kelley.com/FA19_POE_Final/documentation/hardware/assembly/)
- Electrical and Firmware
  - Firmware Overview (https://jonathan-kelley.com/FA19_POE_Final/documentation/ece/firmware/)
  - Sensors (https://jonathan-kelley.com/FA19_POE_Final/documentation/ece/sensors/)
  - Controls and Feedback (https://jonathan-kelley.com/FA19_POE_Final/documentation/ece/controls/)

# Budget

Item | Quantity | Price Per | Price Total
DC Motor 200 RPM | 6 | $15 | $90
DC Motor Controller | 6 | $4 | $24
5mm Shaft | 2 | $8 | $16
3mm Shaft | 1 | $7 | $7
M5 Bearing | 4 | $5 | $20
M3 Bearing | 10 | $7 | $70
Encoder | 6 | $2 | $12
Hardware Kit | 1 | $15 | $10
Total: | | | $249

©2017-2019 — Jonathan Kelley (https://jonathan-kelley.com) and contributors (https://github.com/jkelleyrtp/FA19_POE_Final/graphs/contributors)

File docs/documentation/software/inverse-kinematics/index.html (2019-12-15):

- Overview
  - Overview (https://jonathan-kelley.com/FA19_POE_Final/documentation/overview/overview/)
  - Brainstorming + Inspiration (https://jonathan-kelley.com/FA19_POE_Final/documentation/overview/brainstorming/)
  - Budget (https://jonathan-kelley.com/FA19_POE_Final/documentation/overview/budget/)
- Software
  - Software Overview (https://jonathan-kelley.com/FA19_POE_Final/documentation/software/systems-overview/)
  - Human Tracking (https://jonathan-kelley.com/FA19_POE_Final/documentation/software/human-tracking/)
  - Inverse Kinematics (https://jonathan-kelley.com/FA19_POE_Final/documentation/software/inverse-kinematics/)
  - PyBullet Simulation (https://jonathan-kelley.com/FA19_POE_Final/documentation/software/pybulletsimulation/)
  - Multithreaded Framework (https://jonathan-kelley.com/FA19_POE_Final/documentation/software/multithreading/)
  - Serial Output (https://jonathan-kelley.com/FA19_POE_Final/documentation/software/serialoutput/)
- Hardware
  - High Level Design (https://jonathan-kelley.com/FA19_POE_Final/documentation/hardware/highlevel/)
  - Base Design (https://jonathan-kelley.com/FA19_POE_Final/documentation/hardware/base/)
  - Torso Design (https://jonathan-kelley.com/FA19_POE_Final/documentation/hardware/torso/)
  - Shoulder Design (https://jonathan-kelley.com/FA19_POE_Final/documentation/hardware/shoulder/)
  - Arm Design (https://jonathan-kelley.com/FA19_POE_Final/documentation/hardware/arm/)
  - Assembly (https://jonathan-kelley.com/FA19_POE_Final/documentation/hardware/assembly/)
- Electrical and Firmware
  - Firmware Overview (https://jonathan-kelley.com/FA19_POE_Final/documentation/ece/firmware/)
  - Sensors (https://jonathan-kelley.com/FA19_POE_Final/documentation/ece/sensors/)
  - Controls and Feedback (https://jonathan-kelley.com/FA19_POE_Final/documentation/ece/controls/)

# Inverse Kinematics

## 🔗Inverse Kinematics

Inverse Kinematics is needed to map human movement into robot movement. This is because, calculating joint angles using human extracted joints doesn't translate to robot joint angles. We have different joints than the robot and at different positions and lengths. Instead, using an inverse kinematics solver an articulated body can be programmed to reach a certain target position with its end effector.



In RealSteel's robots, we have the following revolute joints in an arm:

1. Shoulder
2. Proximal
3. Distal



### 🔗How Does It Work?

Given a target position, how can we position the articulated body and all it's joints such that the end effector reaches the target? An inverse kinematics solver answers this question with two categories of solutions:

1. Analytic solutions
2. Approximating solutions

We use ikpy, an inverse kinematics library, that can quickly approximate the solution with an iterative optimizer with regularization for smoothing.



ikpy also can import the kinematic chain to solve as long as the robot is defined in URDF format. Luckily for us, we designed our own robot in OnShape and using onshape-to-robot we can convert our OnShape assembly to URDF robot definition.

### 🔗ikpy Coordinate System

ikpy defines its kinematic chain to start at the origin in a coordinate system that is rotated 90° about the x-axis compared to the Kinect coordinate system. We also run into an issue as the Kinect tracks joint positions with respect to a fixed origin at the center of it's camera lens and not at the base of the kinematic chain - the origin that ikpy expects. Therefore, any target position that we want to solve for with ikpy will be misinterpreted.

The solution is to transform the target joint's (the hand joint) position from the Kinect frame to a frame that has it's origin fixed at the shoulder joint of the arm that is being solved for. The z or depth value is then inverted to place depth in front of the person, and the point is rotated 90° about the x-axis. This way now the kinematic chain and target joint position are in the same frame of reference, and ikpy can solve correctly.



### 🔗The Process

With all the tools in place, we can now proceed with solving for our robot joint angles in real-time in the following steps (note: this is done independently for both arms each)

1. Obtain robot model in URDF format
2. Import model into ikpy and define a base_element to start the kinematic chain at the shoulder joint of an arm
3. Obtain target position from the Kinect → the world coordinates for skeletal joint at the hand for the corresponding arm
4. Perform the necessary transforms to get the target into ikpy coordinate system
5. Solve for joint angles

https://youtu.be/kSUGiyJ5UbY

©2017-2019 — Jonathan Kelley (https://jonathan-kelley.com) and contributors (https://github.com/jkelleyrtp/FA19_POE_Final/graphs/contributors)

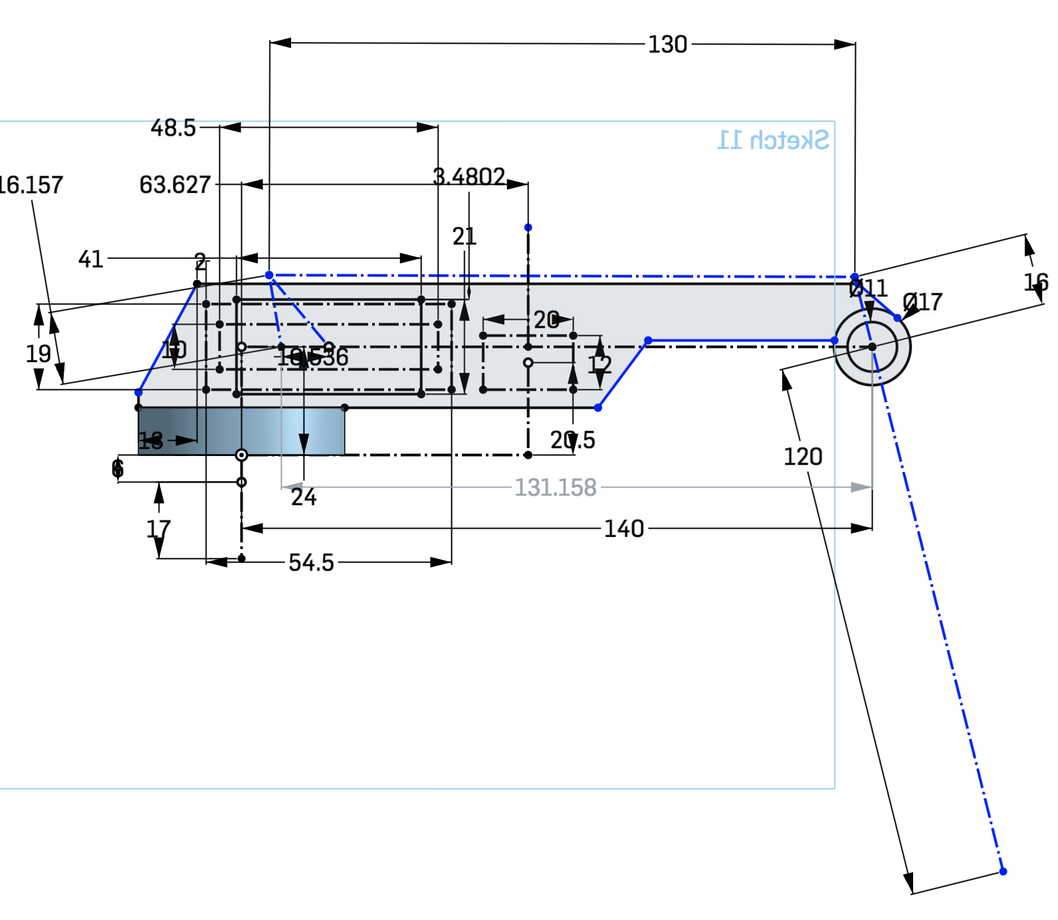
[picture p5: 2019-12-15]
docs/documentation/hardware/arm/Untitled.png

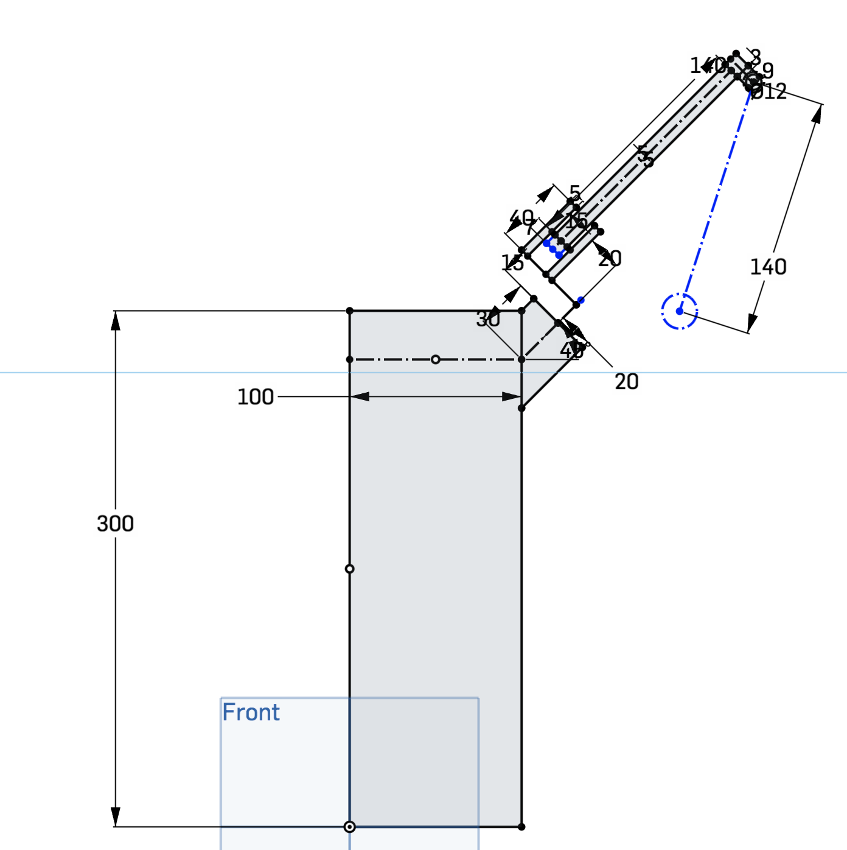
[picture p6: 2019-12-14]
docs/documentation/hardware/highlevel/Untitled.png

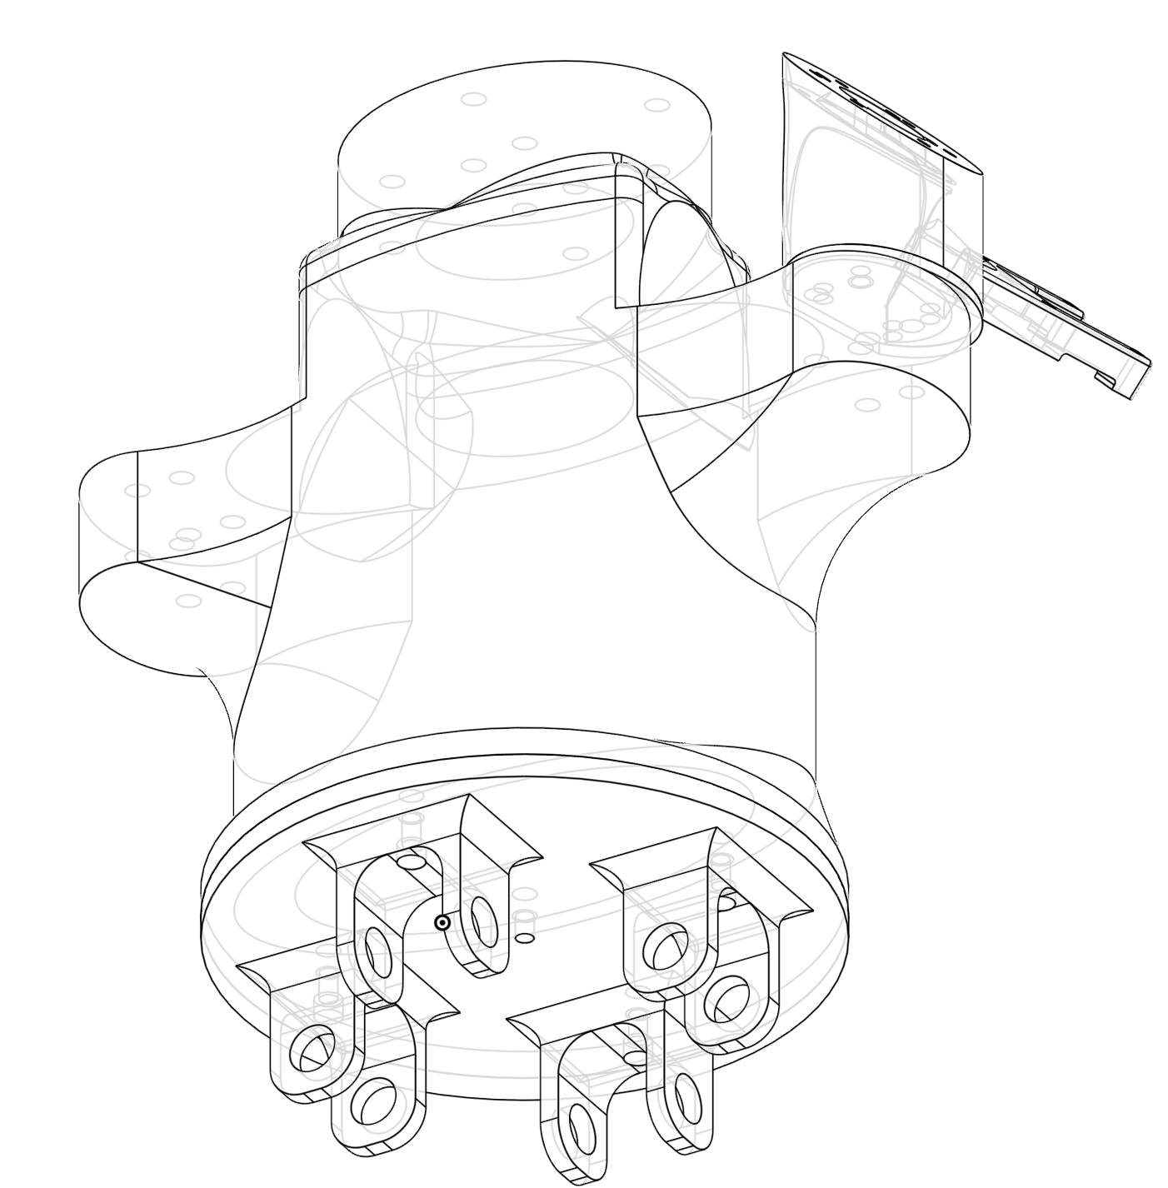
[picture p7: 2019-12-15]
docs/documentation/hardware/torso/Untitled.png

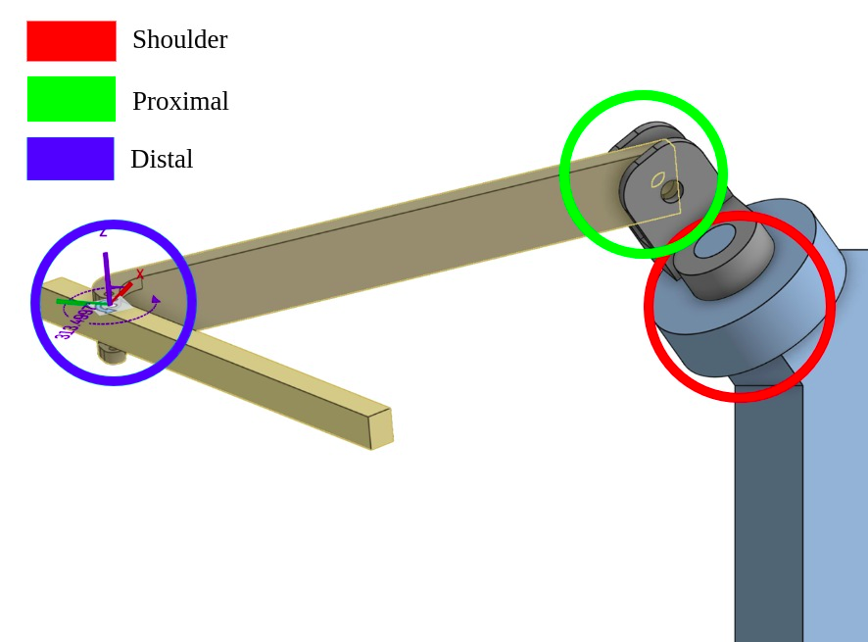
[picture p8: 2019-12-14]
docs/documentation/software/inverse_kinematics/Untitled.png

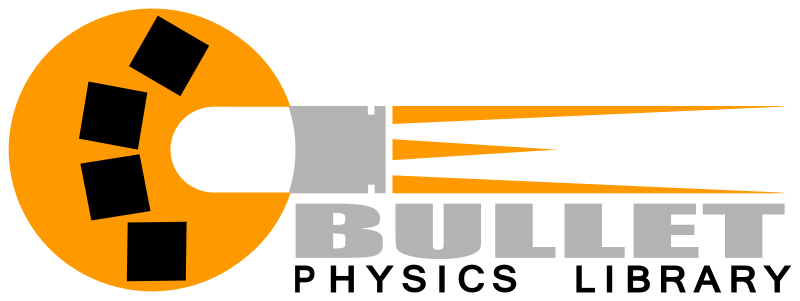
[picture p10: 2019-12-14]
docs/documentation/software/inverse_kinematics/Untitled 3.png

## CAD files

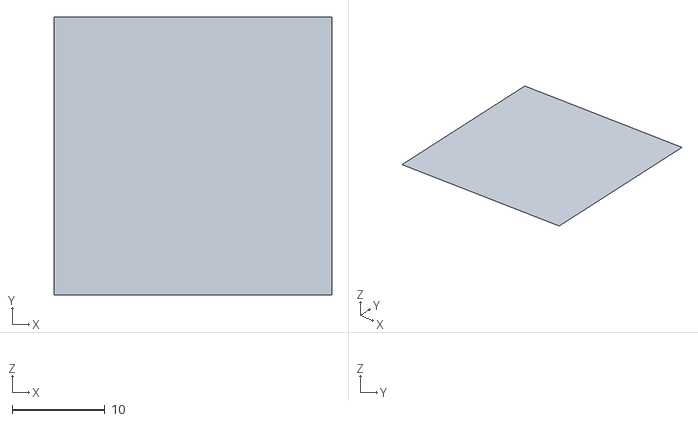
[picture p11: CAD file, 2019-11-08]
robot/environment/plane.obj
30.0 x 30.0 x 0

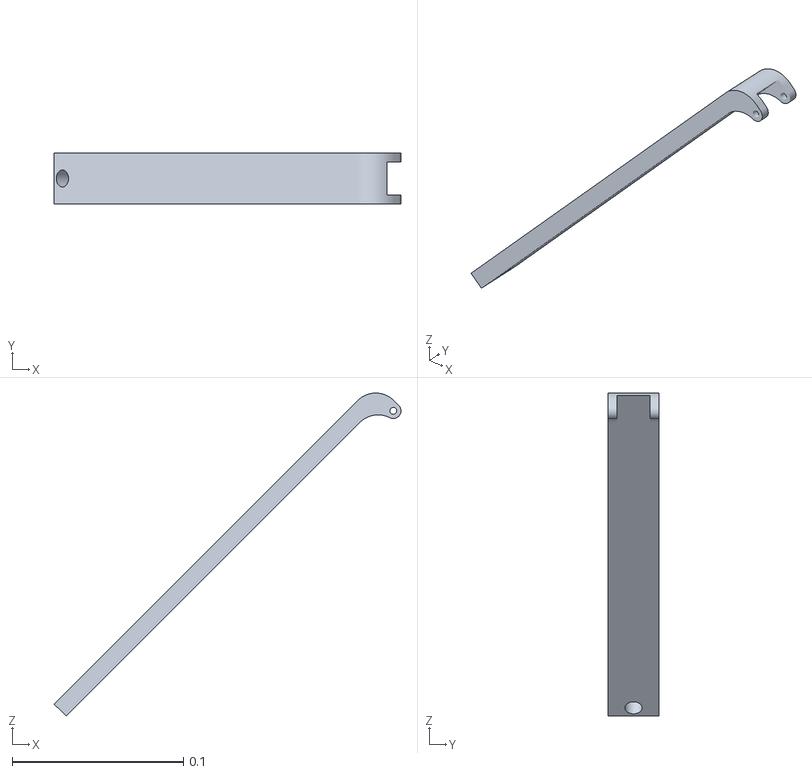
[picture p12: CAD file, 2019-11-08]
robot/part_3.stl
0.203 x 0.03 x 0.189

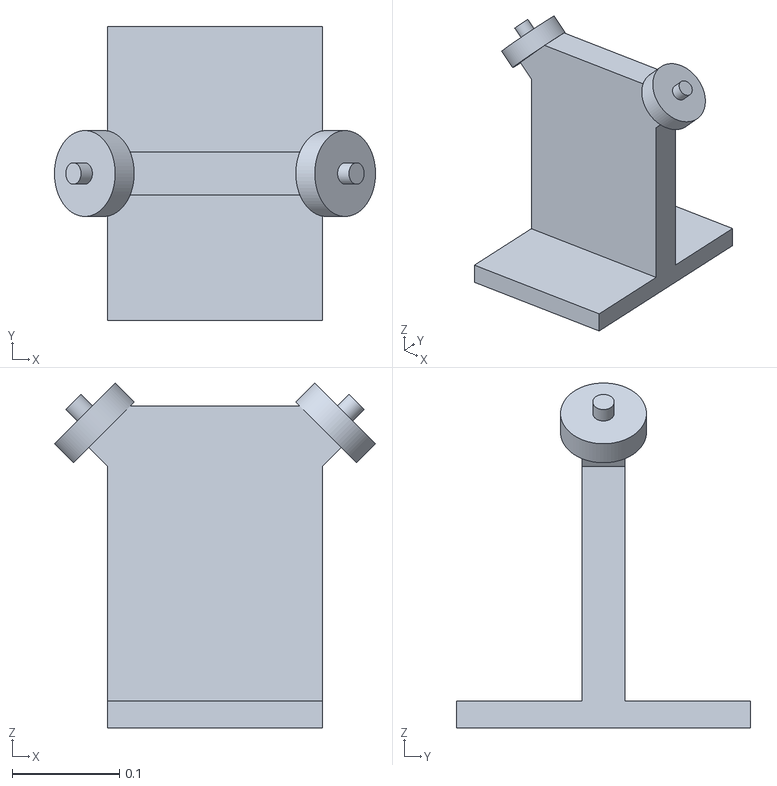
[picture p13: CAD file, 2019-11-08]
robot/torso.stl
0.299 x 0.274 x 0.321

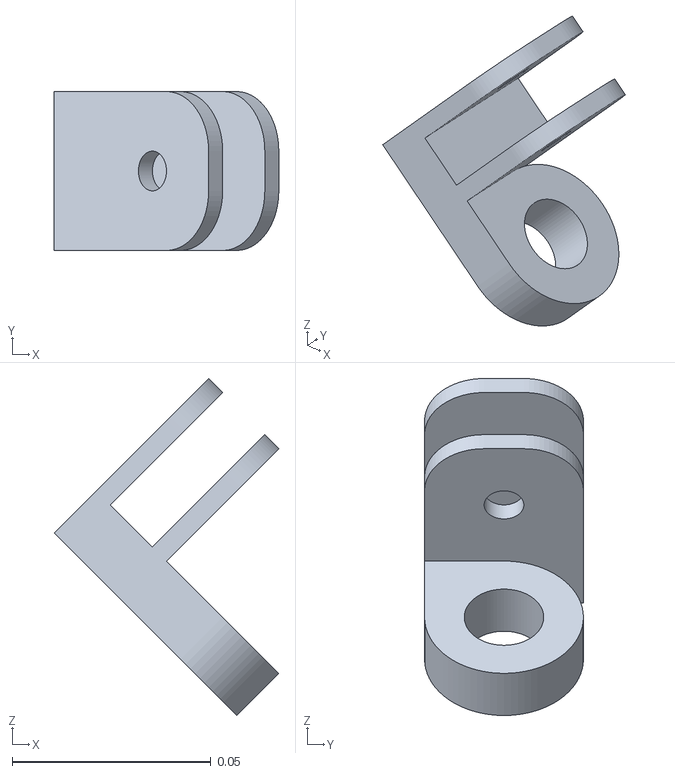
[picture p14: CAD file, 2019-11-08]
robot/part_2.stl
0.0566 x 0.04 x 0.0849

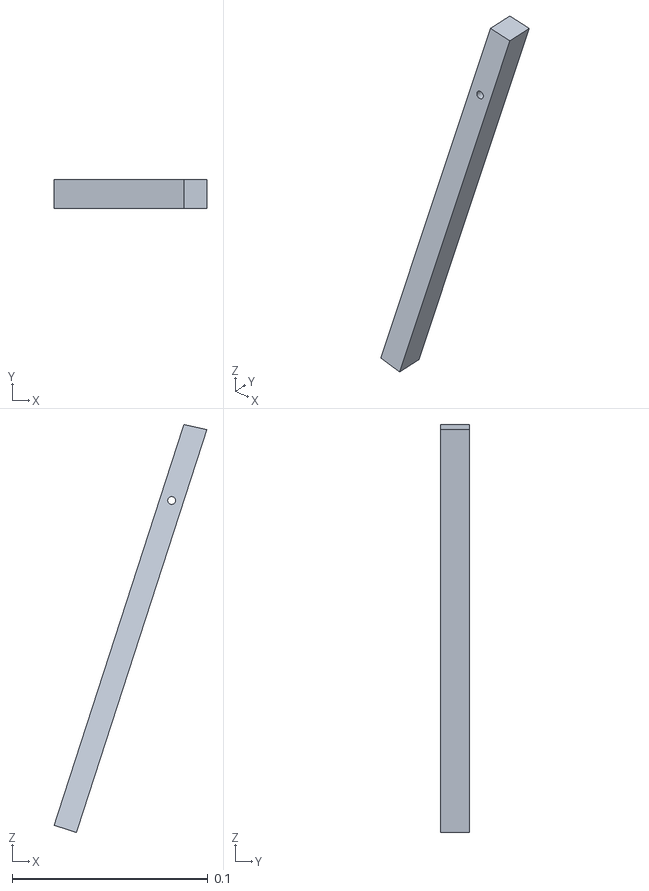
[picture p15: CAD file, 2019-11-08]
robot/part_4.stl
0.0781 x 0.015 x 0.209

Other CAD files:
robot/part_7.stl
robot/part_6.stl
robot/part_5.stl

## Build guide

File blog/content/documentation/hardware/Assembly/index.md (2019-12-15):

+++
title = "Assembly"
weight = 50
+++

Assembly of the Real Steel robots took quite a long time due to the complexity of the subsystems and integration. We spent a considerable amount of time wiring up the sensors and motors and worked from drawings to maintain consistency. Fortunately, we made sure to include fasteners in the modeling process which sped up the process.

<center> {{ resize_image(path="documentation/hardware/Assembly/Untitled.png", width=0, height=500, op="fit_height") }} </center>

<center> {{ resize_image(path="documentation/hardware/Assembly/Untitled 1.png", width=0, height=500, op="fit_height") }} </center>

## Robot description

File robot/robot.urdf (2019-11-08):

<robot name="onshape">
<link name="torso_1">
<inertial>
<origin xyz="0 0 0" rpy="0 0 0" />
<mass value="1e-9" />
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
</inertial>
</link>
<link name="torso_1_0_torso">
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
<inertial>
<origin xyz="5.51967e-18 -1.18625e-17 0.117316" rpy="0 0 0"/>
<mass value="29.6172"/>
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
</inertial>
</link>
<joint name="torso_1_torso_1_0_torso_fixing" type="fixed">
<origin xyz="0 0 0" rpy="0 -0 0" />
<parent link="torso_1" />
<child link="torso_1_0_torso" />
<axis xyz="0 0 0"/>
</joint>

<link name="part_5_1">
<inertial>
<origin xyz="0 0 0" rpy="0 0 0" />
<mass value="1e-9" />
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
</inertial>
</link>
<link name="part_5_1_0_part_5">
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
<inertial>
<origin xyz="0 0 0" rpy="0 0 0"/>
<mass value="0"/>
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
</inertial>
</link>
<joint name="part_5_1_part_5_1_0_part_5_fixing" type="fixed">
<origin xyz="0.13182 -6.93889e-18 -0.303536" rpy="1.11022e-16 -5.55112e-17 5.55112e-17" />
<parent link="part_5_1" />
<child link="part_5_1_0_part_5" />
<axis xyz="0 0 0"/>
</joint>

<link name="part_6_1">
<inertial>
<origin xyz="0 0 0" rpy="0 0 0" />
<mass value="1e-9" />
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
</inertial>
</link>
<link name="part_6_1_0_part_6">
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
<inertial>
<origin xyz="0 0 0" rpy="0 0 0"/>
<mass value="0"/>
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
</inertial>
</link>
<joint name="part_6_1_part_6_1_0_part_6_fixing" type="fixed">
<origin xyz="0.119445 -5.55112e-17 -0.344194" rpy="0 -0 0" />
<parent link="part_6_1" />
<child link="part_6_1_0_part_6" />
<axis xyz="0 0 0"/>
</joint>

<link name="part_7_1">
<inertial>
<origin xyz="0 0 0" rpy="0 0 0" />
<mass value="1e-9" />
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
</inertial>
</link>
<link name="part_7_1_0_part_7">
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
<inertial>
<origin xyz="0 0 0" rpy="0 0 0"/>
<mass value="0"/>
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
</inertial>
</link>
<joint name="part_7_1_part_7_1_0_part_7_fixing" type="fixed">
<origin xyz="0.312839 0.0075 -0.510718" rpy="-2.77556e-17 5.55112e-17 1.38778e-17" />
<parent link="part_7_1" />
<child link="part_7_1_0_part_7" />
<axis xyz="0 0 0"/>
</joint>

<joint name="distal_right" type="revolute">
<origin xyz="-0.193394 -0.0097 0.166524" rpy="2.01609e-16 0.811584 -3.32655e-15" />
<parent link="part_6_1" />
<child link="part_7_1" />
<axis xyz="0 -1 0"/>
<limit effort="1.5" velocity="22" />
<joint_properties friction="0.0"/>
</joint>

<joint name="proximal_right" type="revolute">
<origin xyz="0.0141421 -4.16334e-17 0.0424264" rpy="-0.705905 -0.269757 -0.705905" />
<parent link="part_5_1" />
<child link="part_6_1" />
<axis xyz="0.707107 0 0.707107"/>
<limit effort="1.5" velocity="22" />
<joint_properties friction="0.0"/>
</joint>

<joint name="shoulder_right" type="revolute">
<origin xyz="-0.13182 -2.77556e-17 0.303536" rpy="-0.706606 0.270333 0.706606" />
<parent link="torso_1" />
<child link="part_5_1" />
<axis xyz="0.707107 0 -0.707107"/>
<limit effort="1.5" velocity="22" />
<joint_properties friction="0.0"/>
</joint>

<link name="part_2_1">
<inertial>
<origin xyz="0 0 0" rpy="0 0 0" />
<mass value="1e-9" />
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
</inertial>
</link>
<link name="part_2_1_0_part_2">
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
<inertial>
<origin xyz="0 0 0" rpy="0 0 0"/>
<mass value="0"/>
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
</inertial>
</link>
<joint name="part_2_1_part_2_1_0_part_2_fixing" type="fixed">
<origin xyz="-0.13182 5.55112e-17 -0.303536" rpy="-5.55112e-17 -0 0" />
<parent link="part_2_1" />
<child link="part_2_1_0_part_2" />
<axis xyz="0 0 0"/>
</joint>

<link name="part_3_1">
<inertial>
<origin xyz="0 0 0" rpy="0 0 0" />
<mass value="1e-9" />
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
</inertial>
</link>
<link name="part_3_1_0_part_3">
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
<inertial>
<origin xyz="0 0 0" rpy="0 0 0"/>
<mass value="0"/>
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
</inertial>
</link>
<joint name="part_3_1_part_3_1_0_part_3_fixing" type="fixed">
<origin xyz="-0.119445 -1.38778e-17 -0.344194" rpy="-5.55112e-17 -0 0" />
<parent link="part_3_1" />
<child link="part_3_1_0_part_3" />
<axis xyz="0 0 0"/>
</joint>

<link name="part_4_1">
<inertial>
<origin xyz="0 0 0" rpy="0 0 0" />
<mass value="1e-9" />
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
</inertial>
</link>
<link name="part_4_1_0_part_4">
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
<inertial>
<origin xyz="0 0 0" rpy="0 0 0"/>
<mass value="0"/>
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
</inertial>
</link>
<joint name="part_4_1_part_4_1_0_part_4_fixing" type="fixed">
<origin xyz="-0.312839 0.0075 -0.510718" rpy="0 -0 5.55112e-17" />
<parent link="part_4_1" />
<child link="part_4_1_0_part_4" />
<axis xyz="0 0 0"/>
</joint>

<joint name="distal_left" type="revolute">
<origin xyz="0.193394 -0.0097 0.166524" rpy="1.66533e-16 -7.21645e-16 3.88578e-16" />
<parent link="part_3_1" />
<child link="part_4_1" />
<axis xyz="0 -1 0"/>
<limit effort="1.5" velocity="22" />
<joint_properties friction="0.0"/>
</joint>

<joint name="proximal_left" type="revolute">
<origin xyz="-0.0141421 0 0.0424264" rpy="-7.77156e-16 7.77156e-16 5.55112e-17" />
<parent link="part_2_1" />
<child link="part_3_1" />
<axis xyz="-0.707107 0 0.707107"/>
<limit effort="1.5" velocity="22" />
<joint_properties friction="0.0"/>
</joint>

<joint name="shoulder_left" type="revolute">
<origin xyz="0.13182 -2.77556e-17 0.303536" rpy="-0.752186 -0.309384 -0.752186" />
<parent link="torso_1" />
<child link="part_2_1" />
<axis xyz="0.707107 0 0.707107"/>
<limit effort="1.5" velocity="22" />
<joint_properties friction="0.0"/>
</joint>

</robot>

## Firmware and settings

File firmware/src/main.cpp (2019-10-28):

#include <Arduino.h>
#include <Servo.h>

// Set up the torso commands
#define TORSO_MOTOR_PIN 0
#define TORSO_POS_CMD 10

Servo myservo1;  // create servo object to control a servo
Servo myservo2;  // create servo object to control a servo
Servo myservo3;  // create servo object to control a servo


void setup() {
  Serial.begin(9600); 
  myservo1.attach(11);  // attaches the servo on pin 9 to the servo object
  myservo2.attach(12);  // attaches the servo on pin 9 to the servo object
  myservo3.attach(13);  // attaches the servo on pin 9 to the servo object

}

int pos = 0;    // variable to store the servo position

void loop() {
  for (pos = 60; pos <= 160; pos += 1) { // goes from 0 degrees to 180 degrees
    myservo1.write(pos);
    delay(15);                       // waits 15ms for the servo to reach the position
  }
  for (pos = 120; pos >= 60; pos -= 1) { // goes from 180 degrees to 0 degrees
    myservo1.write(pos);              // tell servo to go to position in variable 'pos'
    delay(15);                       // waits 15ms for the servo to reach 
  }  
  for (pos = 60; pos <= 90; pos += 1) { // goes from 0 degrees to 180 degrees
    myservo1.write(pos);
    delay(15);                       // waits 15ms for the servo to reach the position
  }


  for (pos = 60; pos <= 160; pos += 1) { // goes from 0 degrees to 180 degrees
    myservo2.write(pos);
    myservo3.write(pos);
    delay(15);                       // waits 15ms for the servo to reach the position
  }
  for (pos = 120; pos >= 60; pos -= 1) { // goes from 180 degrees to 0 degrees
    myservo2.write(pos);              // tell servo to go to position in variable 'pos'
    myservo3.write(pos);
    delay(15);                       // waits 15ms for the servo to reach 
  }  




  // if ( Serial.available() ) {
  //   switch( Serial.read() ){
  //     case TORSO_POS_CMD:

  //       break;    

  //     default:


  //       break;
  //   }  
  // }
}

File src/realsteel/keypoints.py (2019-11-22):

import os
import sys
import argparse
import time
import freenect
import cv2
import numpy as np
import pprint
from multiprocessing import Process, Queue

class Pose:
    """Pose estimation class bridging OpenPose and Kinect

    Args:
        params: OpenPose custom params (refer to OpenPose include/openpose/flags.hpp for more parameters)
        camera: kinect camera device index (default: 0)
        model_path: path to OpenPose models installed directory (default: models/)
    """

    def __init__(self, params: dict={}, camera: int=0, model_path: str='/home/richard/Desktop/openpose/models/'):
        try:
            sys.path.append('/usr/local/python')
            from openpose import pyopenpose as op
            self.op = op
        except ImportError as e:
            print('Error: OpenPose library could not be found. Did you enable `BUILD_PYTHON` \
                in CMake and have this Python script in the right folder?')
            raise e

        if not params:
            # Set default parameters for Olin laptops
            params["net_resolution"] = "-1x160"
            params["model_pose"] = "COCO"
            params["tracking"] = "1"
            params["number_people_max"] = "1"
            params["part_candidates"] = True
        
        self.params = params

        # Add model path
        self.params["model_folder"] = model_path

        self.camera = camera

    def get_video(self) -> np.ndarray:
        """Get RGB image from the kinect
        
        Returns:
            numpy array of RGB image

        """
        array, _ = freenect.sync_get_video()
        array = cv2.cvtColor(array, cv2.COLOR_RGB2BGR)
        array = cv2.flip(array, 1)
        return array
    
    def get_depth(self, format=freenect.DEPTH_REGISTERED) -> np.ndarray:
        """Get depth from the kinect
        
        Args:
            format: kinect depth format (default: DEPTH_REGISTERED,
            produces distance in millimeters where (x,y) of depth matches (x,y) of video)
                
        Returns:
            numpy array of depth image

        """
        array, _ = freenect.sync_get_depth(format=format)
        return array

    def jointPoints(self, keypoints, depths: np.ndarray, confidenceThreshold: int=.6) -> dict:
        """Determine joint point cloud

        Args:
            keypoints: OpenPose posecandidates keypoints
            depths: depth image
            confidenceThreshold: any joint above this value is considered (default: .6) 

        Returns:
            dict of joint dictonaries with point cloud (meters) and image coordinates

        """
        COCO_OUTPUT = ['Nose', 'Neck', 'Rsho', 'Relb', 'Rwri', 'Lsho', 'Lelb', 'Lwri','Rhip',\
            'Rkne', 'Rank', 'Lhip', 'Lkne', 'Lank', 'Leye', 'Reye', 'Lear', 'Rear']
        joints = {}
        for idx, joint in enumerate(np.asarray(keypoints)):
            coords = np.asarray(joint[0][0:2]).astype(int) \
                if len(joint) > 0 and joint[0][2] > confidenceThreshold else []
            
            # Ignore empty joints
            if not len(coords):
                joints[COCO_OUTPUT[idx]] = {}
                continue

            # Known openpose bug where it predicts outside frame dimensions
            if coords[0] > 640 and coords[1] > 480:
                print('DEBUG: Openpose predicted joint out of frame')
                joints[COCO_OUTPUT[idx]] = {}
                continue
            
            # Numpy array order is row, col -> y, x
            wz = depths[coords[1], coords[0]]

            # Ignore joints not in depth thresholds
            if wz == 0:
                joints[COCO_OUTPUT[idx]] = {}
                continue
            
            # Get x and y in world coordinates in mm
            wx, wy = freenect.camera_to_world(coords[0], coords[1], wz, self.camera)
            joints[COCO_OUTPUT[idx]] = {'pc': (round(wx/1000, 2), round(wy/1000, 2), wz/1000), 'xy': (coords[0], coords[1])}
        
        return joints

    def launch(self, queue, DEBUG: bool=False):
        q = queue
        p = Process(target=self.runloop, args=(q, DEBUG))
        return p

    def runloop(self, queue: Queue, DEBUG: bool):
        """Start running the pose estimation

        Enqueue current frame's joint information

        Args:
            queue: Queue object to hold joint information
            DEBUG: when true displays kinect RGB and Depth frames with joints superimposed
        
        """
        # Starting OpenPose
        opWrapper = self.op.WrapperPython()
        opWrapper.configure(self.params)
        opWrapper.start()

        while True:
            img = self.get_video()

            # Process Image
            datum = self.op.Datum()
            datum.cvInputData = img
            opWrapper.emplaceAndPop([datum])

            keypoints = datum.poseCandidates

            depths = self.get_depth()

            joints = self.jointPoints(keypoints, depths)
            queue.put(joints)

            if DEBUG:
                # Render OpenPose frame
                im = datum.cvOutputData

                # Display joint values
                font = cv2.FONT_HERSHEY_SIMPLEX
                for name, joint in joints.items():
                    if joint:
                        cv2.putText(im, str(joint['pc']), joint['xy'], font, .5, (0, 255, 0), 1, cv2.LINE_AA)
                
                cv2.imshow('Pose Estimation', im)
                cv2.imshow('Depth image', depths.astype(np.uint8))

                key = cv2.waitKey(1)
                if key == ord('q'):
                    break 
        
        if DEBUG:
            cv2.destroyAllWindows()

if __name__ == '__main__':
    joints = Queue()
    keypoints_proc = Pose().launch(joints, DEBUG=False)
    
    print('Starting pose detection process')

    keypoints_proc.start()

    while True:
        # Get most recent joints point cloud
        if not joints.empty():
            jointsFrame = joints.get()
            pprint.pprint(jointsFrame)
        
        if not keypoints_proc.is_alive():
            print('Pose detection process killed')
            break

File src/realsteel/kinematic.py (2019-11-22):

import numpy as np
import matplotlib.pyplot as plt
from ikpy.chain import Chain
from ikpy.link import OriginLink, URDFLink
from ikpy import plot_utils

# Solve the kinematic 



class KSOLVER:
    def __init__(self, *args, **kwargs):
        self.chain = Chain(name='left_arm', links=[
            OriginLink(),
            URDFLink(
            name="shoulder_left",
            translation_vector=[0.13182, -2.77556e-17, 0.303536],
            orientation=[-0.752186, -0.309384, -0.752186],
            rotation=[0.707107, 0, 0.707107],
            ),
            URDFLink(
            name="proximal_left",
            translation_vector=[-0.0141421, 0, 0.0424264],
            orientation=[-7.77156e-16, 7.77156e-16, 5.55112e-17],
            rotation=[-0.707107, 0, 0.707107],
            ),
            URDFLink(
            name="distal_left",
            translation_vector=[0.193394, -0.0097, 0.166524],
            orientation=[1.66533e-16, -7.21645e-16, 3.88578e-16],
            rotation=[0, -1, 0],
            )
        ])

    def solve(self, wrist_postion):
        """Performs inverse kinematics and returns joint angles in rads
        
        For now uses one target vector at the wrist position for inverse kinematics.
        For the future, should use additional target vectors and match the elbow

        """
        # TODO: Fix coordinate system transform for extra degree of freedom rotation
        # Setup target vector with target position at wrist
        target_vector = np.array([wrist_postion[0], wrist_postion[1], wrist_postion[2]])
        target_frame = np.eye(4) 
        target_frame[:3, 3] = target_vector

        joint_angles = self.chain.inverse_kinematics(target_frame)[1:3]
        print('Joint angles:', joint_angles)
        print('Computed position vector:', self.chain.forward_kinematics(self.chain.inverse_kinematics(target_frame))[:3, 3], \
            'Original position vector:', target_frame[:3, 3])

        joints = self.chain.inverse_kinematics(target_frame)[1:3]

        return np.array([0, joints[1]])


class ArmJoints():
    def __init__(self, shoulder, proximal, distal):
        self.shoulder = shoulder
        self.proximal = proximal
        self.distal = distal

    def serialize(self):
        return bytes('#{},{}!'.format(self.shoulder, self.proximal), encoding="ascii")

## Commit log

2019-11-01 Updating angles for keypoints of joints on openpose code; removed visualization for frame rate optimizaiton
2019-11-08 python base upgraded
    [part_5.stl, part_6.stl, part_7.stl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]
2019-11-08 Spinning arms from parallel processes
    [part_2.stl, part_3.stl, part_4.stl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]
2019-11-08 Fix the type of value that get's passed through
    [joint_input.py, visualizer.py]
